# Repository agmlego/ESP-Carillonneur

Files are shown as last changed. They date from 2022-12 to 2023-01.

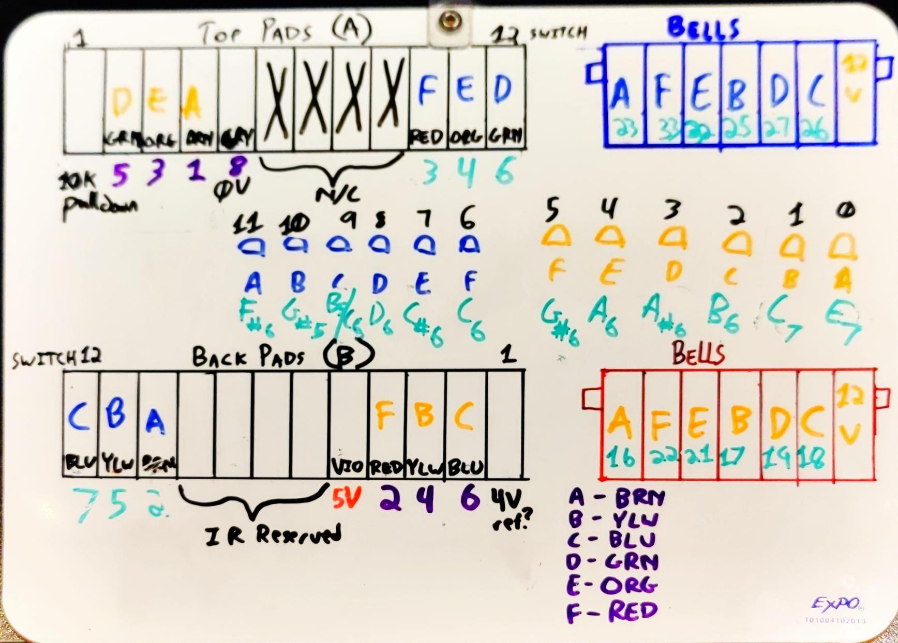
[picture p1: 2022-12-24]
Images/aus-200 reverse engineering notes.jpg

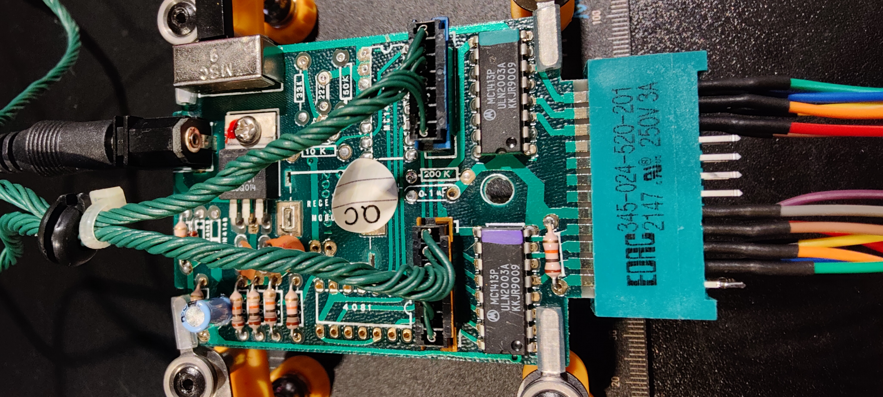
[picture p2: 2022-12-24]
Images/IMG20221223194835.jpg

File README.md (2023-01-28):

ESP Carillonneur
================

A project to ESP-ify the "Caroling Christmas Bells" product line from Ye Merrie Minstrel, in particular the variant with part number AUS-200.

## Goals:

* Maintain function with the existing OEM music cartridges
* Allow MIDI control over WiFi
* Allow MIDI control from local storage (SD? Flash?)

## Pinout

### Blue (Right) Bell Connector
0. `IO23` (Furthest from connector)
1. `IO21`
2. `IO18`
3. `IO5`
4. `IO19`
5. `IO22` (Closest to connector)

### Orange (Left) Bell Connector
0. `IO16` (Furthest from connector)
1. `IO4`
2. `IO26`
3. `IO25`
4. `IO27`
5. `IO17` (Closest to connector)

### IR expansion Interface
0. `IO32`
1. `IO34`
2. `IO33`
3. `IO35`

### Mainboard Detection Signals
* "Detect" (on the AUS-200, a 10k pulldown): `IO39`
* "Ref" (on the AUS-200, a 4V reference from resistor divider and IN4148): `IO36`

## Case

The case design uses four M2 heat-set inserts ([94459A120](https://www.mcmaster.com/94459A120/)) and four M2 x 5mm button-head screws ([92095A452]https://www.mcmaster.com/92095A452/). The existing sliding door needs a 1/4" diameter slot cut in the back wall, 1/2" in from the mating edge. This will clear the antenna port.

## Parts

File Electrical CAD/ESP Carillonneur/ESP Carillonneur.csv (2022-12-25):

Source: | D:\documents\projects\ESP Carillonneur\Electrical CAD\ESP Carillonneur\ESP Carillonneur.kicad_sch
Date: | 2022-12-25 15:49:38
Tool: | Eeschema (6.0.8)
Generator: | C:\Program Files\KiCad\6.0\bin\scripting\plugins/bom_csv_grouped_by_value_with_fp.py
Component Count: | 27
Ref | Qnty | Value | Cmp name | Footprint | Description | Vendor
3V3_LED1, | 1 | RED LED | LED | LED_SMD:LED_0603_1608Metric | Light emitting diode
C1, | 1 | 10µF | C | Capacitor_SMD:CP_Elec_4x4.5 | Unpolarized capacitor
C2, | 1 | 1nF | C | Capacitor_SMD:C_0603_1608Metric | Unpolarized capacitor
C3, | 1 | 22µF | C | Capacitor_SMD:CP_Elec_4x4.5 | Unpolarized capacitor
C4, C5, C6, | 3 | 0.1µF | C | Capacitor_SMD:C_0603_1608Metric | Unpolarized capacitor
H1, H2, H3, H4, | 4 | MountingHole | MountingHole | MountingHole:MountingHole_2.2mm_M2 | Mounting Hole without connection
J1, | 1 | 345-024-520-201 | Conn_02x12_Row_Letter_First | Footprints:EEC12DRAN | Generic connector, double row, 02x12, row letter first pin numbering scheme (pin number consists of a letter for the row and a number for the pin index in this row. a1, ..., aN; b1, ..., bN), script generated (kicad-library-utils/schlib/autogen/connector/)
J2, | 1 | Micro_SD_Card_Det | Micro_SD_Card_Det | Connector_Card:microSD_HC_Hirose_DM3AT-SF-PEJM5 | Micro SD Card Socket with card detection pins
JTAG1, | 1 | Conn_02x05_Odd_Even | Conn_02x05_Odd_Even | Connector:Tag-Connect_TC2050-IDC-NL_2x05_P1.27mm_Vertical | Generic connector, double row, 02x05, odd/even pin numbering scheme (row 1 odd numbers, row 2 even numbers), script generated (kicad-library-utils/schlib/autogen/connector/)
R1, | 1 | 2K2 | R | Resistor_SMD:R_0603_1608Metric | Resistor
R2, R5, R8, | 3 | 4K7 | R | Resistor_SMD:R_0603_1608Metric | Resistor
R3, R4, R6, R7, | 4 | 10K | R | Resistor_SMD:R_0603_1608Metric | Resistor
R9, | 1 | 9K1 | R | Resistor_SMD:R_0603_1608Metric | Resistor
SW1, | 1 | SW_Push | SW_Push | Button_Switch_SMD:Panasonic_EVQPUL_EVQPUC | Push button switch, generic, two pins
U1, | 1 | LD1117S33TR_SOT223 | LD1117S33TR_SOT223 | Package_TO_SOT_SMD:SOT-223-3_TabPin2 | 800mA Fixed Low Drop Positive Voltage Regulator, Fixed Output 3.3V, SOT-223
U2, | 1 | ESP32-WROOM-32U | ESP32-WROOM-32U | RF_Module:ESP32-WROOM-32U | RF Module, ESP32-D0WD SoC, Wi-Fi 802.11b/g/n, Bluetooth, BLE, 32-bit, 2.7-3.6V, external antenna, SMD
UART1, | 1 | Conn_02x03_Odd_Even | Conn_02x03_Odd_Even | Connector:Tag-Connect_TC2030-IDC-NL_2x03_P1.27mm_Vertical | Generic connector, double row, 02x03, odd/even pin numbering scheme (row 1 odd numbers, row 2 even numbers), script generated (kicad-library-utils/schlib/autogen/connector/)

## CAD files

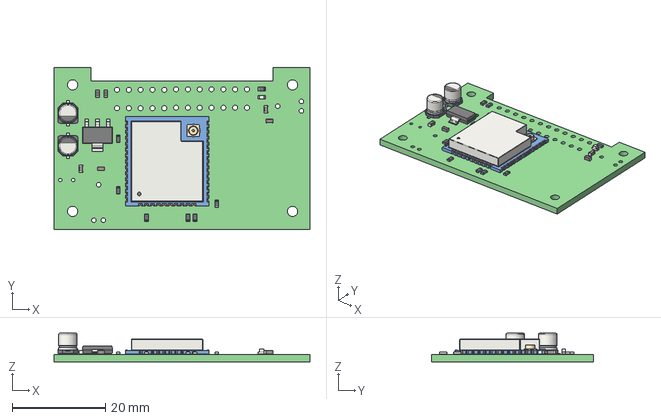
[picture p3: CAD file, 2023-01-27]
Electrical CAD/ESP Carillonneur/ESP Carillonneur.step
55.0 x 34.9 x 6.15 mm
_autosave-ESP Carillonneur PCB

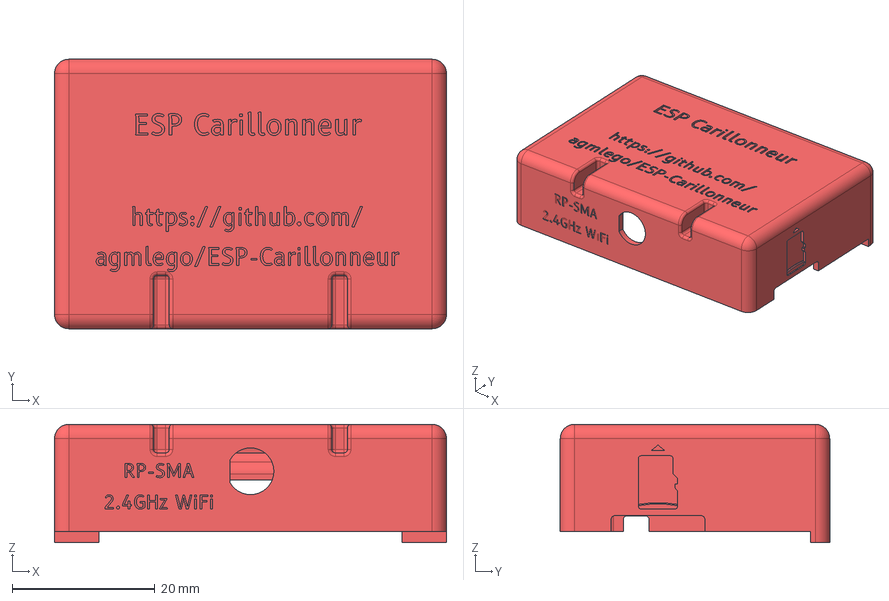
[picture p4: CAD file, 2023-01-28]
Mechanical CAD/case.stp
55.0 x 37.8 x 16.6 mm

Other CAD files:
Mechanical CAD/AUS-200/aus-200_bottom.ipt
Mechanical CAD/AUS-200/aus-200_top.ipt
Mechanical CAD/AUS-200/sliding_door.ipt
Mechanical CAD/DM3AT-SF-PEJM5/DM3AT-SF-PEJM5.ipt
Mechanical CAD/EEC12DRAN.ipt
Mechanical CAD/ESP Carillonneur/ESP Carillonneur.iam
Mechanical CAD/EVQPU-LC-02K/EVQPU-LC-02K.ipt
Mechanical CAD/case.obj
Mechanical CAD/case.stl
Mechanical CAD/rp-sma_nut.ipt
Mechanical CAD/rp-sma_pigtail.ipt
Mechanical CAD/rp-sma_washer.ipt

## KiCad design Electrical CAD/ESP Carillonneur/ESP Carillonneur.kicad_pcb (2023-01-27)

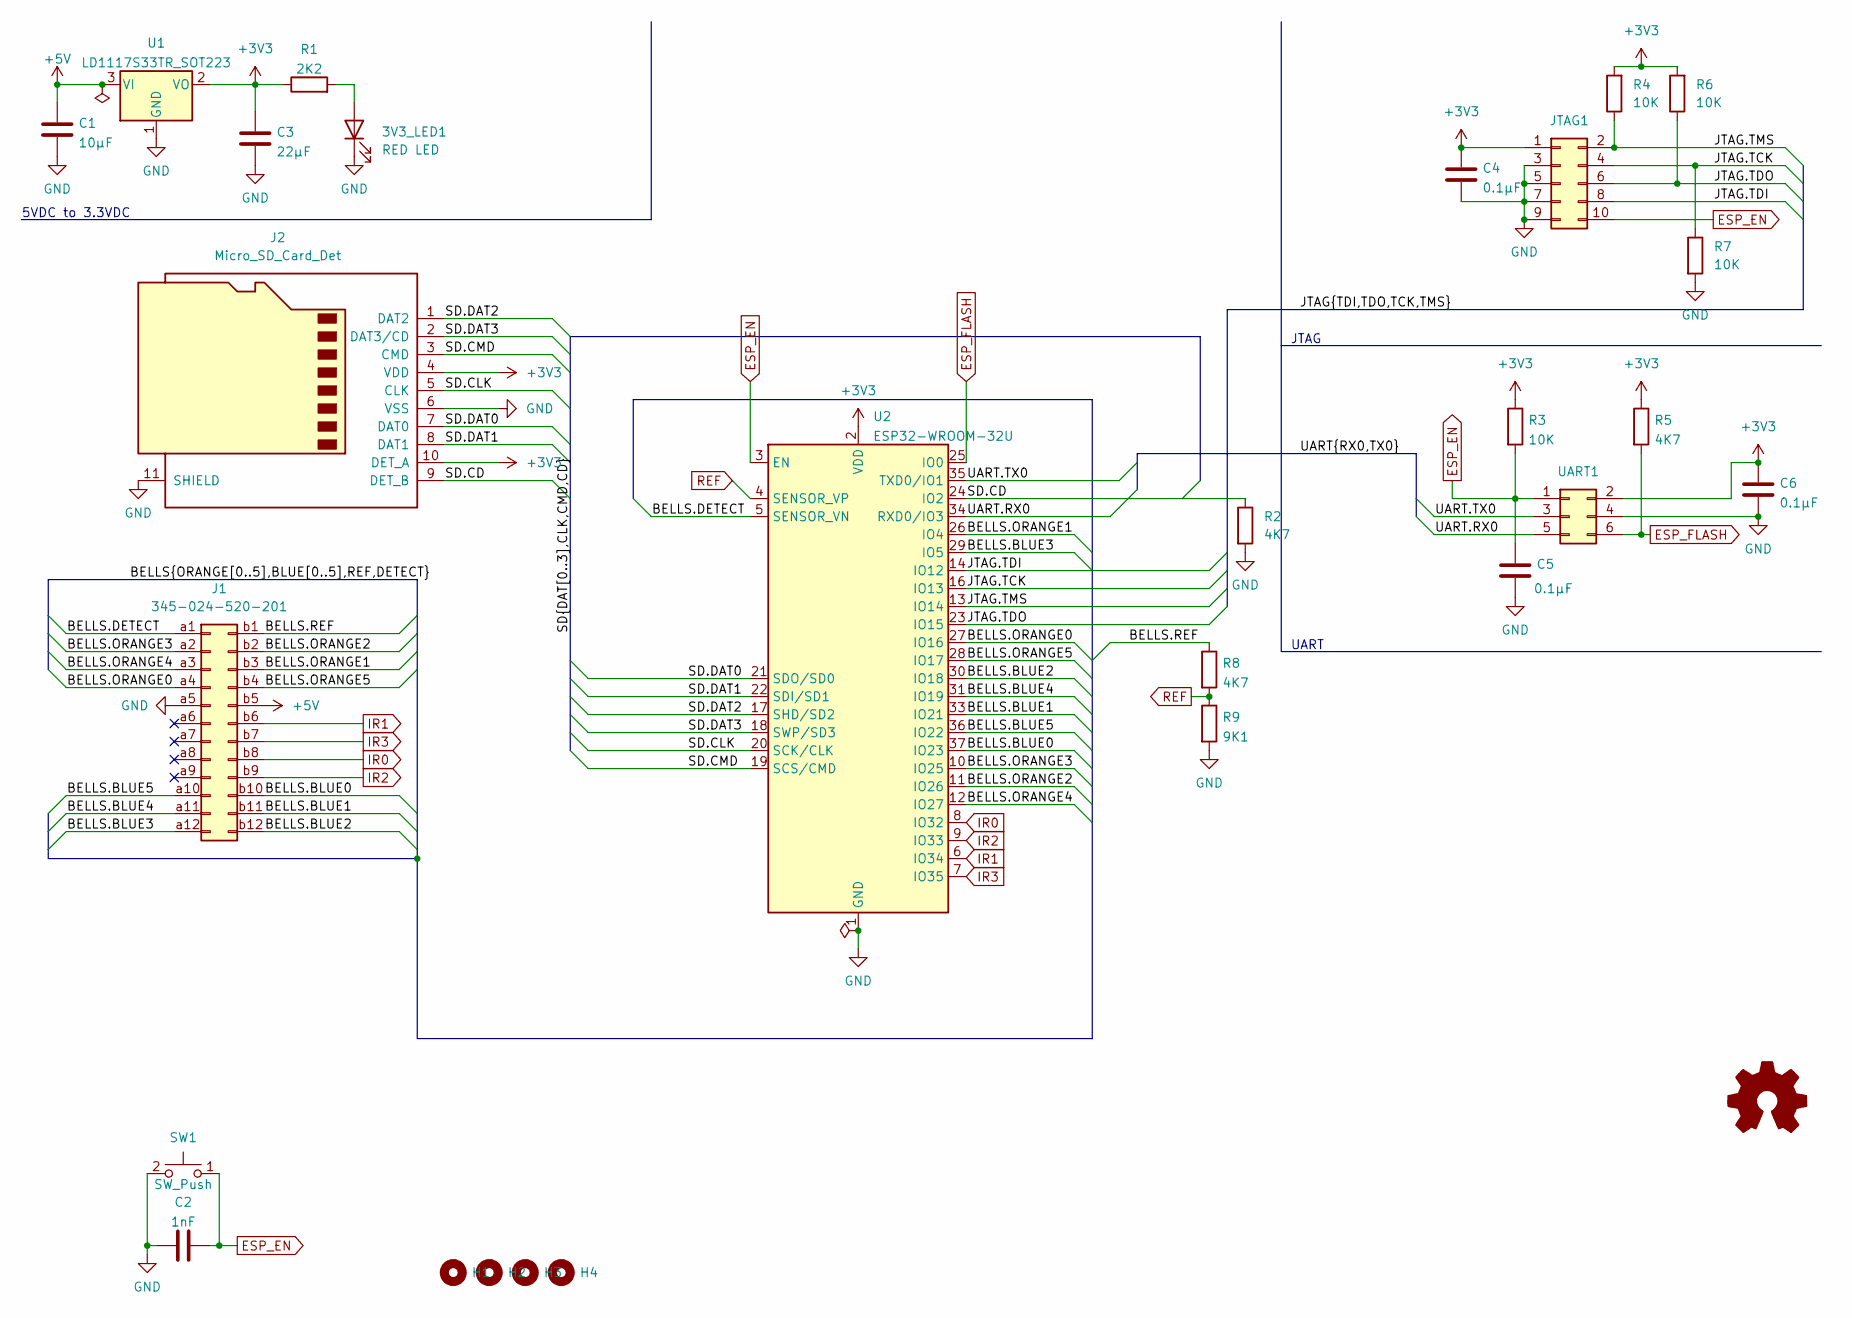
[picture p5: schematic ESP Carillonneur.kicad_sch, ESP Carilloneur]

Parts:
3V3_LED1: RED LED; LED_0603_1608Metric
C1: 10µF; CP_Elec_4x4.5
C2: 1nF; C_0603_1608Metric
C3: 22µF; CP_Elec_4x4.5
C4, C5, C6: 0.1µF; C_0603_1608Metric
H1, H2, H3, H4: MountingHole; MountingHole_2.2mm_M2
J1: 345-024-520-201; EEC12DRAN
J2: Micro_SD_Card_Det; microSD_HC_Hirose_DM3AT-SF-PEJM5
JTAG1: Conn_02x05_Odd_Even; Tag-Connect_TC2050-IDC-NL_2x05_P1.27mm_Vertical
R1: 2K2; R_0603_1608Metric
R2, R5, R8: 4K7; R_0603_1608Metric
R3, R4, R6, R7: 10K; R_0603_1608Metric
R9: 9K1; R_0603_1608Metric
SW1: SW_Push; Panasonic_EVQPUL_EVQPUC
U1: LD1117S33TR_SOT223; SOT-223-3_TabPin2
U2: ESP32-WROOM-32U
UART1: Conn_02x03_Odd_Even; Tag-Connect_TC2030-IDC-NL_2x03_P1.27mm_Vertical

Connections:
+3V3: C3.1, C4.1, C6.1, J2.4 (VDD), J2.10 (DET_A), JTAG1.1, R1.1, R3.1, R4.2, R5.1, R6.2, U1.2 (VO), U2.2 (VDD), UART1.2
+5V: C1.1, J1.b5, U1.3 (VI)
/BELLS.BLUE0: J1.b10, U2.37 (IO23)
/BELLS.BLUE1: J1.b11, U2.33 (IO21)
/BELLS.BLUE2: J1.b12, U2.30 (IO18)
/BELLS.BLUE3: J1.a12, U2.29 (IO5)
/BELLS.BLUE4: J1.a11, U2.31 (IO19)
/BELLS.BLUE5: J1.a10, U2.36 (IO22)
/BELLS.DETECT: J1.a1, U2.5 (SENSOR_VN)
/BELLS.ORANGE0: J1.a4, U2.27 (IO16)
/BELLS.ORANGE1: J1.b3, U2.26 (IO4)
/BELLS.ORANGE2: J1.b2, U2.11 (IO26)
/BELLS.ORANGE3: J1.a2, U2.10 (IO25)
/BELLS.ORANGE4: J1.a3, U2.12 (IO27)
/BELLS.ORANGE5: J1.b4, U2.28 (IO17)
/BELLS.REF: J1.b1, R8.1
/JTAG.TCK: JTAG1.4, R7.1, U2.16 (IO13)
/JTAG.TDI: JTAG1.8, U2.14 (IO12)
/JTAG.TDO: JTAG1.6, R6.1, U2.23 (IO15)
/JTAG.TMS: JTAG1.2, R4.1, U2.13 (IO14)
/SD.CD: J2.9 (DET_B), R2.1, U2.24 (IO2)
/SD.CLK: J2.5 (CLK), U2.20 (SCK/CLK)
/SD.CMD: J2.3 (CMD), U2.19 (SCS/CMD)
/SD.DAT0: J2.7 (DAT0), U2.21 (SDO/SD0)
/SD.DAT1: J2.8 (DAT1), U2.22 (SDI/SD1)
/SD.DAT2: J2.1 (DAT2), U2.17 (SHD/SD2)
/SD.DAT3: J2.2 (DAT3/CD), U2.18 (SWP/SD3)
/UART.RX0: U2.34 (RXD0/IO3), UART1.5
/UART.TX0: U2.35 (TXD0/IO1), UART1.3
ESP_EN: C2.2, C5.1, JTAG1.10, R3.2, SW1.1, U2.3 (EN), UART1.1
ESP_FLASH: R5.2, U2.25 (IO0), UART1.6
GND: 3V3_LED1.1 (K), C1.2, C2.1, C3.2, C4.2, C5.2, C6.2, J1.a5, J2.6 (VSS), J2.11 (SHIELD), JTAG1.3, JTAG1.5, JTAG1.7, JTAG1.9, R2.2, R7.2, R9.2, SW1.2, U1.1 (GND), U2.1 (GND), U2.15 (GND), U2.38 (GND), U2.39 (GND), UART1.4
IR0: J1.b8, U2.8 (IO32)
IR1: J1.b6, U2.6 (IO34)
IR2: J1.b9, U2.9 (IO33)
IR3: J1.b7, U2.7 (IO35)
unnamed: 3V3_LED1.2 (A), R1.2
REF: R8.2, R9.1, U2.4 (SENSOR_VP)

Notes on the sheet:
5VDC to 3.3VDC
JTAG
UART

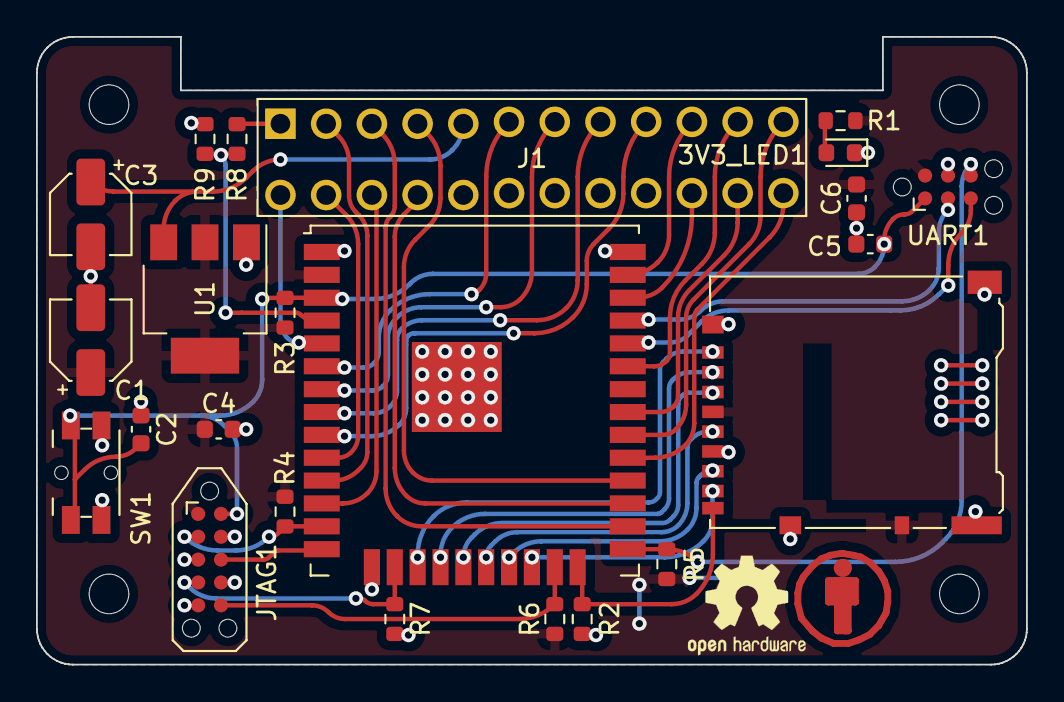
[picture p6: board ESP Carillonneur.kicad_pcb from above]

Board: 2 copper layers, 55.0 x 34.9 mm, 30 parts (1 on the bottom side), 38 nets.

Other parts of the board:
CC_LOGO: Symbol_CC-Attribution_CopperTop_Small
KiCAD_LOGO: KiCad-Logo2_5mm_SilkScreen
OSHW_LOGO: OSHW-Logo2_7.3x6mm_SilkScreen

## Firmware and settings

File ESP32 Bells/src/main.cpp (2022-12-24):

#include <Arduino.h>
#include "bells.h"

uint8_t bell;

void setup()
{
  Serial.begin(115200);
  Serial.println("Setting up bells!");
  for (bell = 0; bell < NUM_bellS; ++bell)
  {
    pinMode(bells[bell], OUTPUT);
    Serial.print(bell_notes[bell]);
    Serial.print(" ");
  }
  Serial.println(" Done!");
  bell = 0;
}

void loop()
{
  Serial.print("Ringing ");
  Serial.print(bell_notes[bell]);
  Serial.print("! ");
  ringbell(bell++);
  Serial.println("DONE");
  delayMicroseconds(1000 * 1000);
  if (bell >= NUM_bellS)
  {
    Serial.println("Resetting bells!");
    bell = 0;
  }
}

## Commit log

2022-12-24 Initial commit
    Reverse-engineering data and schematic, in preparation for ESP cartridge design.
    [Bells AUS-200.kicad_pcb, Bells AUS-200.kicad_sch]
2022-12-24 Rename Mainboard project.
    [AUS-200 Mainboard.kicad_pcb, AUS-200 Mainboard.kicad_sch]
2022-12-24 Schematic design for ESP32-WROOM-32U cartridge
    [ESP Carillonneur.kicad_pcb, ESP Carillonneur.kicad_sch]
2022-12-24 Changed case because apparently this is not a constant...
2022-12-24 Reworked some pins for better routing; beginning of board art.
    [ESP Carillonneur.kicad_pcb, ESP Carillonneur.kicad_sch]
2022-12-25 Added voltage divider for BELLS.REF, more routing
    [ESP Carillonneur.kicad_pcb, ESP Carillonneur.kicad_sch]
2022-12-25 Final bopard routing and silk placement.
    [ESP Carillonneur.kicad_pcb]
2022-12-25 Print readiness and BOMs
    [ESP Carillonneur.csv, ESP Carillonneur.kicad_pcb, ESP Carillonneur.kicad_sch]
2023-01-27 Revised board to fit existing case
    [ESP Carillonneur.kicad_pcb, ESP Carillonneur.kicad_sch]
2023-01-27 Changed pinout in README to match new board revision
2023-01-27 Rounded corners, updated BOM
    [ESP Carillonneur.kicad_pcb, ESP Carillonneur.step]
2023-01-28 Mechanical design for case
    [DM3AT-SF-PEJM5.ipt, EEC12DRAN.ipt, ESP Carillonneur.iam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]
2023-01-28 Added notes about case hardware.
2023-01-28 Final case updates.
    [ESP Carillonneur.iam]
